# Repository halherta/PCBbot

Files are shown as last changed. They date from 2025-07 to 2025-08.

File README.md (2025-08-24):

# Introducing PCBbot!
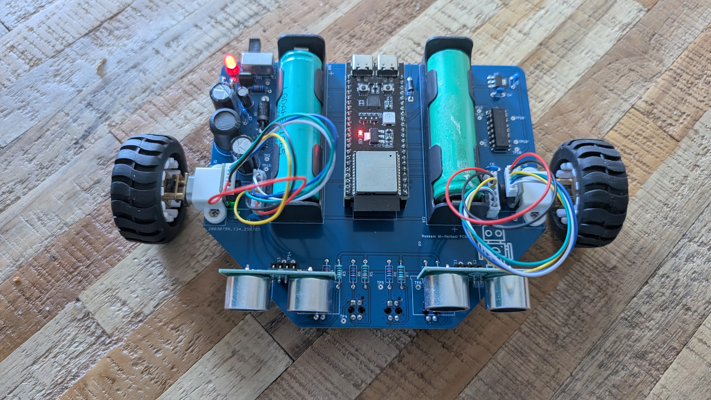
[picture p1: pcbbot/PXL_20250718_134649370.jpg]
pcbbot top view


The PCBBot leverages the PCB itself as the chassis. This reduces cost significantly. It also means that the two motors and the caster wheel would have to be mounted on the PCB itself, in addition to the batteries and all the other components...

For more info have a look at the write up on my [blog entry](https://hussamtalkstech.com/introducing-pcbbot/)

In this Github repo, you'll find my PCBBot KiCAD PCB design freely available (MIT License) along with a Digikey bill of materials (BOM) (caster wheel, motor brackets and motors not included) and MicroPython code. I’m also providing my [custom symbol and footprint libraries in this repo](https://github.com/halherta/mykicadlibrary). Feel free to make your own version of the PCBBot as is or modify it to suit your needs. Have fun!

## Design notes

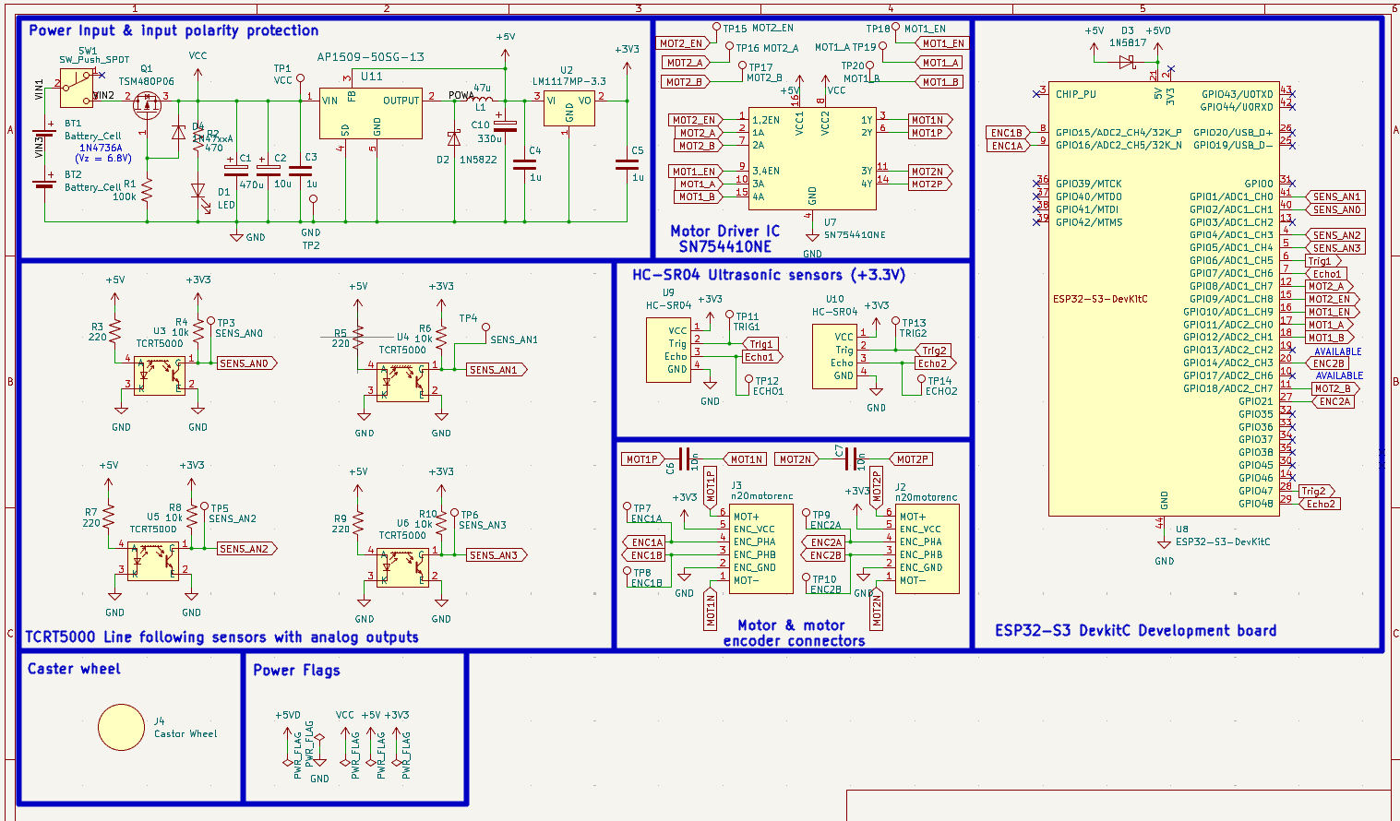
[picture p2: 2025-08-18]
pcbbot/pcbbot_schem.png

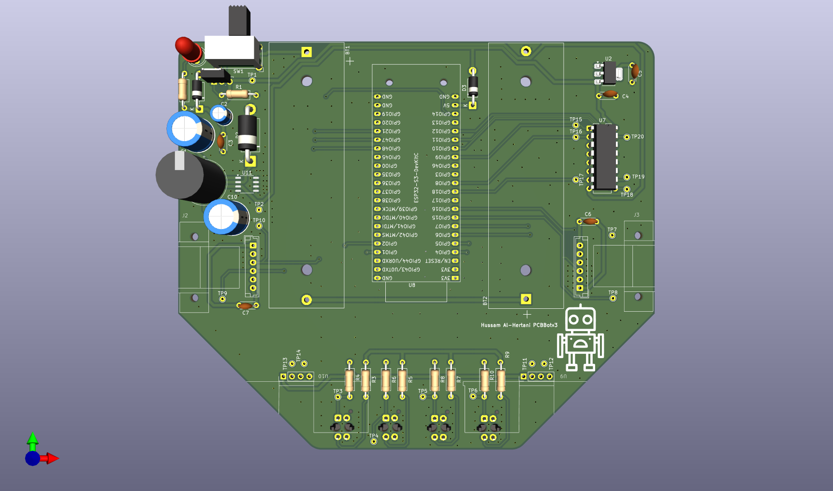
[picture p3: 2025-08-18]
pcbbot/PCBbot.png

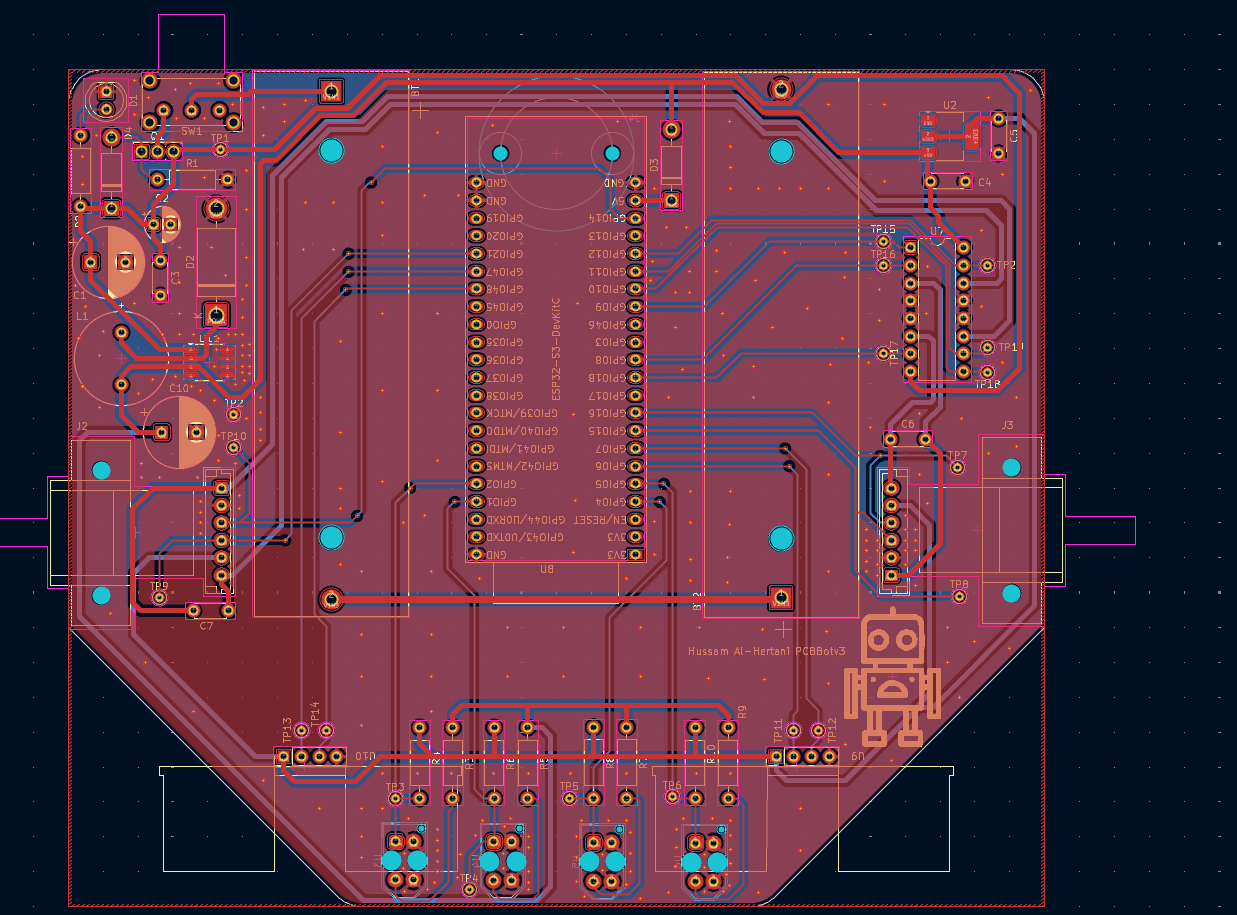
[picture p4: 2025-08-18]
pcbbot/pcbbotpcb.png

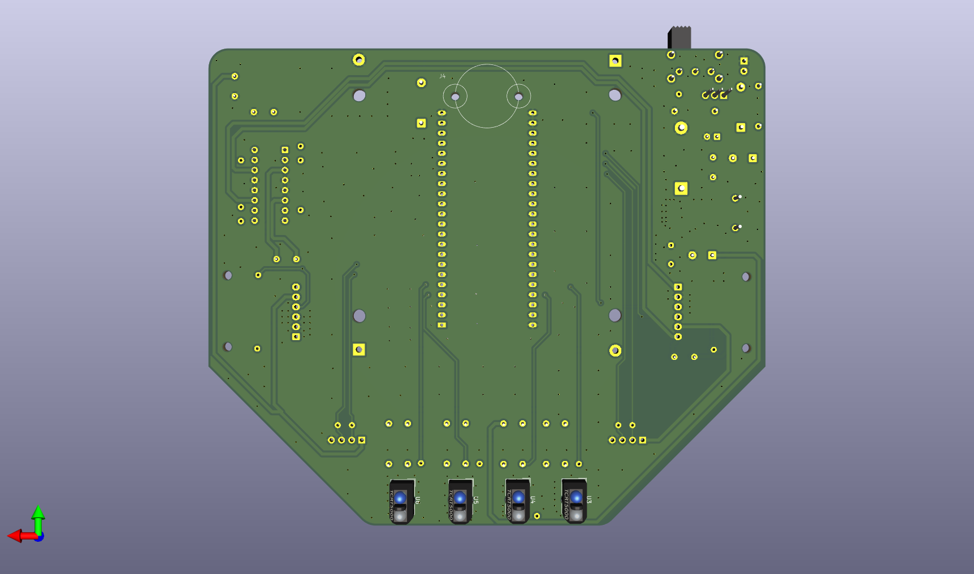
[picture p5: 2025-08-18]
pcbbot/PCBbot2.png

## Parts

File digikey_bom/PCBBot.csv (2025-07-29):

Index | Manufacturer Part Number | Manufacturer Name | Description | Availability | Stock Status | Attrition % | Requested Quantity 1 | Pack Quantity 1 | Pack Type 1 | Digi-Key Part Number 1 | Unit Price 1 | Extended Price 1 | Minimum Order Quantity 1 | Product Notes
1 | EHR-6 | JST Sales America Inc. | CONN RCPT HSG 6POS 2.50MM | 287,103 | In Stock
2 | B6B-EH-A | JST Sales America Inc. | CONN HEADER VERT 6POS 2.5MM | 10,232 | In Stock |  | 4 | 4 | Bulk | 455-1615-ND | 0.27000 | $1.08 | 1
3 | ESP32-S3-DEVKITC-1-N8R8 | Espressif Systems | ESP32-S3-WROOM-1-N8R8 DEV BRD | 0 | Normally Stocking
4 | SN754410NE | Texas Instruments | IC HALF-H DRIVER 36V 16-PDIP | 5,366 | In Stock |  | 1 | 1 | Tube | 296-9911-5-ND | 4.52000 | $4.52 | 1
5 | EG1224 | E-Switch | SWITCH SLIDE SPDT 500MA 15V | 5,229 | In Stock |  | 1 | 1 | Bulk | EG2585-ND | 1.48000 | $1.48 | 1
6 | PPPC221LFBN-RC | Sullins Connector Solutions | CONN HDR 22POS 0.1 GOLD PCB | 2,121 | In Stock |  | 2 | 2 | Tray | S7055-ND | 1.78000 | $3.56 | 1
7 | TCRT5000 | Vishay Semiconductor Opto Division | SENSOR OPTO TRANS 15MM REFL PCB | 2,885 | In Stock |  | 5 | 5 | Tube | 751-1033-5-ND | 1.60400 | $8.02 | 1
8 | TSM480P06CH X0G | Taiwan Semiconductor Corporation | MOSFET P-CHANNEL 60V 20A TO251 | 3,349 | In Stock |  | 1 | 1 | Tube | TSM480P06CHX0G-ND | 1.80000 | $1.80 | 1
9 | WP7113ID | Kingbright | LED RED DIFFUSED T-1 3/4 T/H | 96,702 | In Stock |  | 1 | 1 | Bulk | 754-1264-ND | 0.32000 | $0.32 | 1
10 | MFR-25FRF52-100K | YAGEO | RES 100K OHM 1% 1/4W AXIAL | 80,329 | In Stock |  | 1 | 1 | Cut Tape (CT) | 13-MFR-25FRF52-100KCT-ND | 0.14000 | $0.14 | 1
11 | MFR-25FTE52-470R | YAGEO | RES 470 OHM 1% 1/4W AXIAL | 0 | Normally Stocking |  | 1 | 1 | Cut Tape (CT) | 13-MFR-25FTE52-470RCT-ND | 0.14000 | $0.14 | 1
12 | 35ZLH470MEFC10X16 | Rubycon | CAP ALUM 470UF 20% 35V RADIAL TH | 191,971 | In Stock |  | 1 | 1 | Bulk | 1189-1890-ND | 1.02000 | $1.02 | 1
13 | FG24X7R1H105KRT06 | TDK Corporation | CAP CER 1UF 50V X7R RADIAL | 57,348 | In Stock |  | 3 | 3 | Cut Tape (CT) | 445-173374-1-ND | 0.70000 | $2.10 | 1
14 | 1N4734A | onsemi | DIODE ZENER 5.6V 1W DO41 | 8,168 | In Stock |  | 1 | 1 | Bulk | 1N4734AFS-ND | 0.32000 | $0.32 | 1
15 | BK-18650-PC2 | MPD (Memory Protection Devices) | BATTERY HOLDER 18650 PC PIN | 2,467 | In Stock |  | 2 | 2 | Tray | BK-18650-PC2-ND | 4.76000 | $9.52 | 1
16 | EEU-EB1H100SH | Panasonic Electronic Components | CAP ALUM 10UF 20% 50V RADIAL TH | 384 | In Stock |  | 1 | 1 | Cut Tape (CT) | P19607CT-ND | 0.42000 | $0.42 | 1
17 | LM1117MPX-3.3/NOPB | Texas Instruments | IC REG LIN 3.3V 800MA SOT-223-4 | 22,991 | In Stock |  | 1 | 1 | Cut Tape (CT) | LM1117MPX-3.3/NOPBCT-ND | 1.55000 | $1.55 | 1
18 | 1N5817-T | Diodes Incorporated | DIODE SCHOTTKY 20V 1A DO41 | 58,119 | In Stock |  | 1 | 1 | Cut Tape (CT) | 1N5817DICT-ND | 0.32000 | $0.32 | 1
19 | MFR-25FRF52-10K | YAGEO | RES 10K OHM 1% 1/4W AXIAL | 118,267 | In Stock |  | 10 | 10 | Cut Tape (CT) | 13-MFR-25FRF52-10KCT-ND | 0.05600 | $0.56 | 1
20 | FG18X7R1H103KNT06 | TDK Corporation | CAP CER 10000PF 50V X7R RADIAL | 11,857 | In Stock |  | 2 | 2 | Cut Tape (CT) | 445-173264-1-ND | 0.30000 | $0.60 | 1
21 | PPPC041LFBN-RC | Sullins Connector Solutions | CONN HDR 4POS 0.1 GOLD PCB | 19,116 | In Stock |  | 2 | 2 | Box | S7037-ND | 0.55000 | $1.10 | 1
22 | 4007 | Adafruit Industries LLC | ULT SEN TX/RX 3V/5.5V | 273 | In Stock
23 | SEH-001T-P0.6 | JST Sales America Inc. | CONN SOCKET 22-30AWG CRIMP TIN | 77,300 | In Stock - Value Added
24 | AIUR-06-470K | Abracon LLC | FIXED IND 47UH 3.2A 63 MOHM TH | 2,962 | In Stock |  | 1 | 1 | Bulk | 535-13031-ND | 1.33000 | $1.33 | 1
25 | AP1509-50SG-13 | Diodes Incorporated | IC REG BUCK 5V 2A 8SOP | 38,507 | In Stock |  | 1 | 1 | Cut Tape (CT) | AP1509-50SGDICT-ND | 1.86000 | $1.86 | 1
26 | 1N5822RL | STMicroelectronics | DIODE SCHOTTKY 40V 3A DO201AD | 19,311 | In Stock |  | 1 | 1 | Cut Tape (CT) | 497-14742-1-ND | 0.37000 | $0.37 | 1
27 | LR1F220R | TE Connectivity Passive Product | RES 220 OHM 1% 0.6W AXIAL | 13,524 | In Stock |  | 10 | 10 | Cut Tape (CT) | 1712-LR1F220RCT-ND | 0.04300 | $0.43 | 1
28 | 35ZLH330MEFC10X12.5 | Rubycon | CAP ALUM 330UF 20% 35V RADIAL TH | 18,236 | In Stock |  | 1 | 1 | Bulk | 1189-1891-ND | 0.89000 | $0.89 | 1

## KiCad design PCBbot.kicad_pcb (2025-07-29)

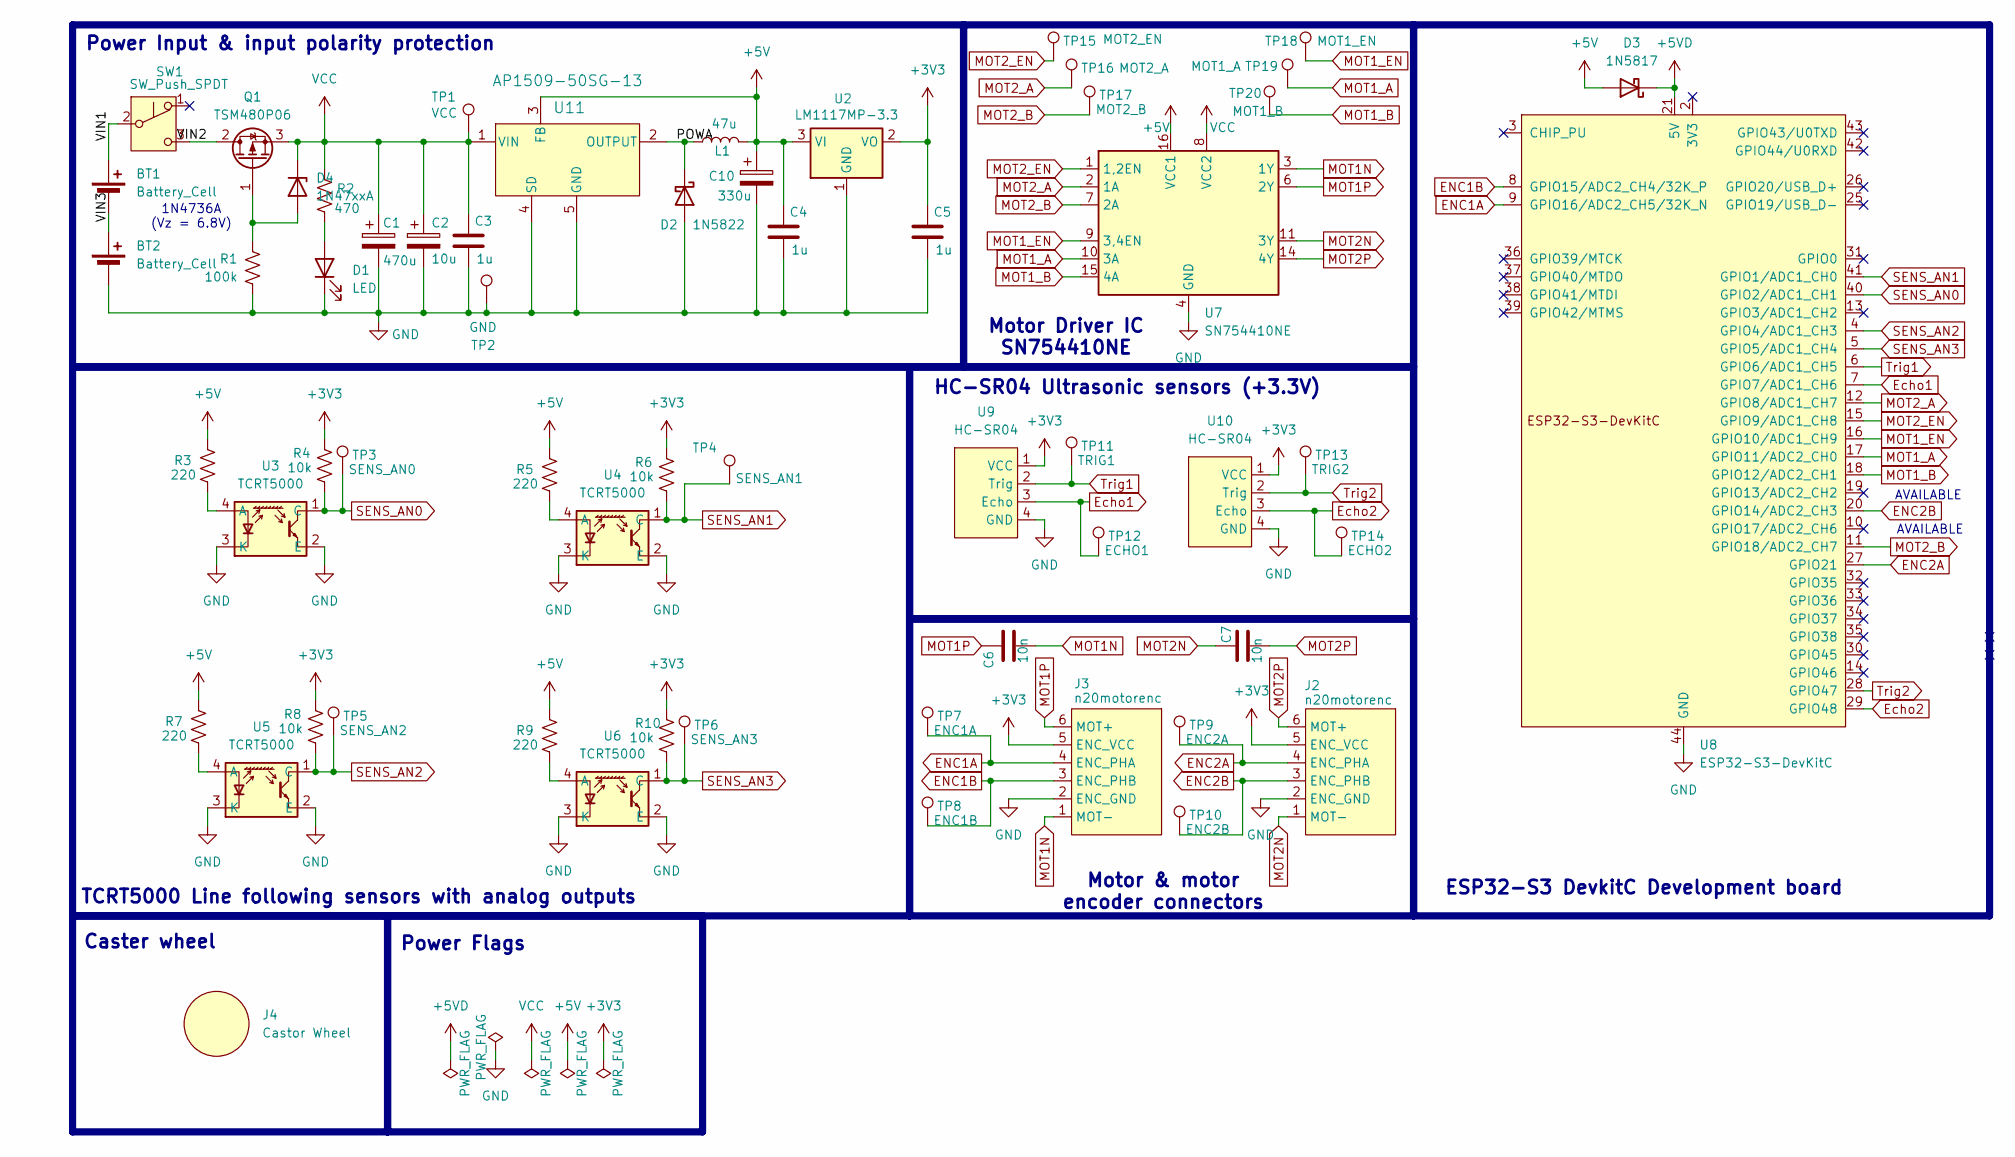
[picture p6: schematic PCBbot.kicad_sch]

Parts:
BT1, BT2: Battery_Cell; BatteryHolder_MPD_BK-18650-PC2
C1: 470u; CP_Radial_D10.0mm_P5.00mm
C2: 10u; CP_Radial_D5.0mm_P2.50mm
C3, C4, C5: 1u; C_Disc_D4.3mm_W1.9mm_P5.00mm
C6, C7: 10n; C_Disc_D4.3mm_W1.9mm_P5.00mm
C10: 330u; CP_Radial_D10.0mm_P5.00mm
D1: LED; LED_D5.0mm
D2: 1N5822; D_DO-201AD_P15.24mm_Horizontal
D3: 1N5817; D_DO-41_SOD81_P10.16mm_Horizontal
D4: 1N47xxA; D_DO-41_SOD81_P10.16mm_Horizontal
J2, J3: n20motorenc; n20motorencv2
J4: Castor Wheel; N20CasterSteelBall-Mini
L1: 47u; AIUR-06_ABRv2
Q1: TSM480P06; TO-251-3_Vertical
R1: 100k; R_Axial_DIN0207_L6.3mm_D2.5mm_P10.16mm_Horizontal
R2: 470; R_Axial_DIN0207_L6.3mm_D2.5mm_P10.16mm_Horizontal
R3, R5, R7, R9: 220; R_Axial_DIN0207_L6.3mm_D2.5mm_P10.16mm_Horizontal
R4, R6, R8, R10: 10k; R_Axial_DIN0207_L6.3mm_D2.5mm_P10.16mm_Horizontal
SW1: SW_Push_SPDT; SW_E-Switch_EG1224_SPDT_Angled
TP1: VCC; TestPoint_THTPad_D1.5mm_Drill0.7mm
TP2: GND; TestPoint_THTPad_D1.5mm_Drill0.7mm
TP3: SENS_AN0; TestPoint_THTPad_D1.5mm_Drill0.7mm
TP4: SENS_AN1; TestPoint_THTPad_D1.5mm_Drill0.7mm
TP5: SENS_AN2; TestPoint_THTPad_D1.5mm_Drill0.7mm
TP6: SENS_AN3; TestPoint_THTPad_D1.5mm_Drill0.7mm
TP7: ENC1A; TestPoint_THTPad_D1.5mm_Drill0.7mm
TP8: ENC1B; TestPoint_THTPad_D1.5mm_Drill0.7mm
TP9: ENC2A; TestPoint_THTPad_D1.5mm_Drill0.7mm
TP10: ENC2B; TestPoint_THTPad_D1.5mm_Drill0.7mm
TP11: TRIG1; TestPoint_THTPad_D1.5mm_Drill0.7mm
TP12: ECHO1; TestPoint_THTPad_D1.5mm_Drill0.7mm
TP13: TRIG2; TestPoint_THTPad_D1.5mm_Drill0.7mm
TP14: ECHO2; TestPoint_THTPad_D1.5mm_Drill0.7mm
TP15: MOT2_EN; TestPoint_THTPad_D1.5mm_Drill0.7mm
TP16: MOT2_A; TestPoint_THTPad_D1.5mm_Drill0.7mm
TP17: MOT2_B; TestPoint_THTPad_D1.5mm_Drill0.7mm
TP18: MOT1_EN; TestPoint_THTPad_D1.5mm_Drill0.7mm
TP19: MOT1_A; TestPoint_THTPad_D1.5mm_Drill0.7mm
TP20: MOT1_B; TestPoint_THTPad_D1.5mm_Drill0.7mm
U2: LM1117MP-3.3; SOT-223-3_TabPin2
U3, U4, U5, U6: TCRT5000; Vishay_TCRT5000
U7: SN754410NE; DIP-16_W7.62mm
U8: ESP32-S3-DevKitC
U9, U10: HC-SR04
U11: AP1509-50SG-13; SOP-8_3.9x4.9mm_P1.27mm

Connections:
+3V3: C5.1, J2.5 (ENC_VCC), J3.5 (ENC_VCC), R4.1, R6.1, R8.1, R10.1, U2.2 (VO), U9.1 (VCC), U10.1 (VCC)
+5V: C4.1, C10.1, D3.2 (A), L1.2, R3.1, R5.1, R7.1, R9.1, U2.3 (VI), U7.16 (VCC1), U11.3 (FB)
+5VD: D3.1 (K), U8.21 (5V)
/POWA: D2.1 (K), L1.1, U11.2 (OUTPUT)
/VIN1: BT1.1 (+), SW1.2 (B)
/VIN2: Q1.2 (D), SW1.3 (C)
/VIN3: BT1.2 (-), BT2.1 (+)
ENC1A: J3.4 (ENC_PHA), TP7.1, U8.9 (GPIO16/ADC2_CH5/32K_N)
ENC1B: J3.3 (ENC_PHB), TP8.1, U8.8 (GPIO15/ADC2_CH4/32K_P)
ENC2A: J2.4 (ENC_PHA), TP9.1, U8.27 (GPIO21)
ENC2B: J2.3 (ENC_PHB), TP10.1, U8.20 (GPIO14/ADC2_CH3)
Echo1: TP12.1, U8.7 (GPIO7/ADC1_CH6), U9.3 (Echo)
Echo2: TP14.1, U8.29 (GPIO48), U10.3 (Echo)
GND: BT2.2 (-), C1.2, C2.2, C3.2, C4.2, C5.2, C10.2, D1.1 (K), D2.2 (A), J2.2 (ENC_GND), J3.2 (ENC_GND), R1.2, TP2.1, U2.1 (GND), U3.2 (E), U3.3 (K), U4.2 (E), U4.3 (K), U5.2 (E), U5.3 (K), U6.2 (E), U6.3 (K), U7.4 (GND), U7.5 (GND), U7.12 (GND), U7.13 (GND), U8.22 (GND), U8.23 (GND), U8.24 (GND), U8.44 (GND), U9.4 (GND), U10.4 (GND), U11.4 (SD), U11.5 (GND), U11.6 (GND), U11.7 (GND), U11.8 (GND)
MOT1N: C6.2, J3.1 (MOT-), U7.3 (1Y)
MOT1P: C6.1, J3.6 (MOT+), U7.6 (2Y)
MOT1_A: TP19.1, U7.10 (3A), U8.17 (GPIO11/ADC2_CH0)
MOT1_B: TP20.1, U7.15 (4A), U8.18 (GPIO12/ADC2_CH1)
MOT1_EN: TP18.1, U7.9 (3,4EN), U8.16 (GPIO10/ADC1_CH9)
MOT2N: C7.1, J2.1 (MOT-), U7.11 (3Y)
MOT2P: C7.2, J2.6 (MOT+), U7.14 (4Y)
MOT2_A: TP16.1, U7.2 (1A), U8.12 (GPIO8/ADC1_CH7)
MOT2_B: TP17.1, U7.7 (2A), U8.11 (GPIO18/ADC2_CH7)
MOT2_EN: TP15.1, U7.1 (1,2EN), U8.15 (GPIO9/ADC1_CH8)
unnamed: D1.2 (A), R2.2
unnamed: D4.2 (A), Q1.1 (G), R1.1
unnamed: R3.2, U3.4 (A)
unnamed: R5.2, U4.4 (A)
unnamed: R7.2, U5.4 (A)
unnamed: R9.2, U6.4 (A)
SENS_AN0: R4.2, TP3.1, U3.1 (C), U8.40 (GPIO2/ADC1_CH1)
SENS_AN1: R6.2, TP4.1, U4.1 (C), U8.41 (GPIO1/ADC1_CH0)
SENS_AN2: R8.2, TP5.1, U5.1 (C), U8.4 (GPIO4/ADC1_CH3)
SENS_AN3: R10.2, TP6.1, U6.1 (C), U8.5 (GPIO5/ADC1_CH4)
Trig1: TP11.1, U8.6 (GPIO6/ADC1_CH5), U9.2 (Trig)
Trig2: TP13.1, U8.28 (GPIO47), U10.2 (Trig)
VCC: C1.1, C2.1, C3.1, D4.1 (K), Q1.3 (S), R2.1, TP1.1, U7.8 (VCC2), U11.1 (VIN)

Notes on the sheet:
HC-SR04 Ultrasonic sensors (+3.3V)
Power Input & input polarity protection
Motor Driver IC SN754410NE
Motor & motor encoder connectors
AVAILABLE
Caster wheel
1N4736A (Vz = 6.8V)
ESP32-S3 DevkitC Development board
TCRT5000 Line following sensors with analog outputs
Power Flags

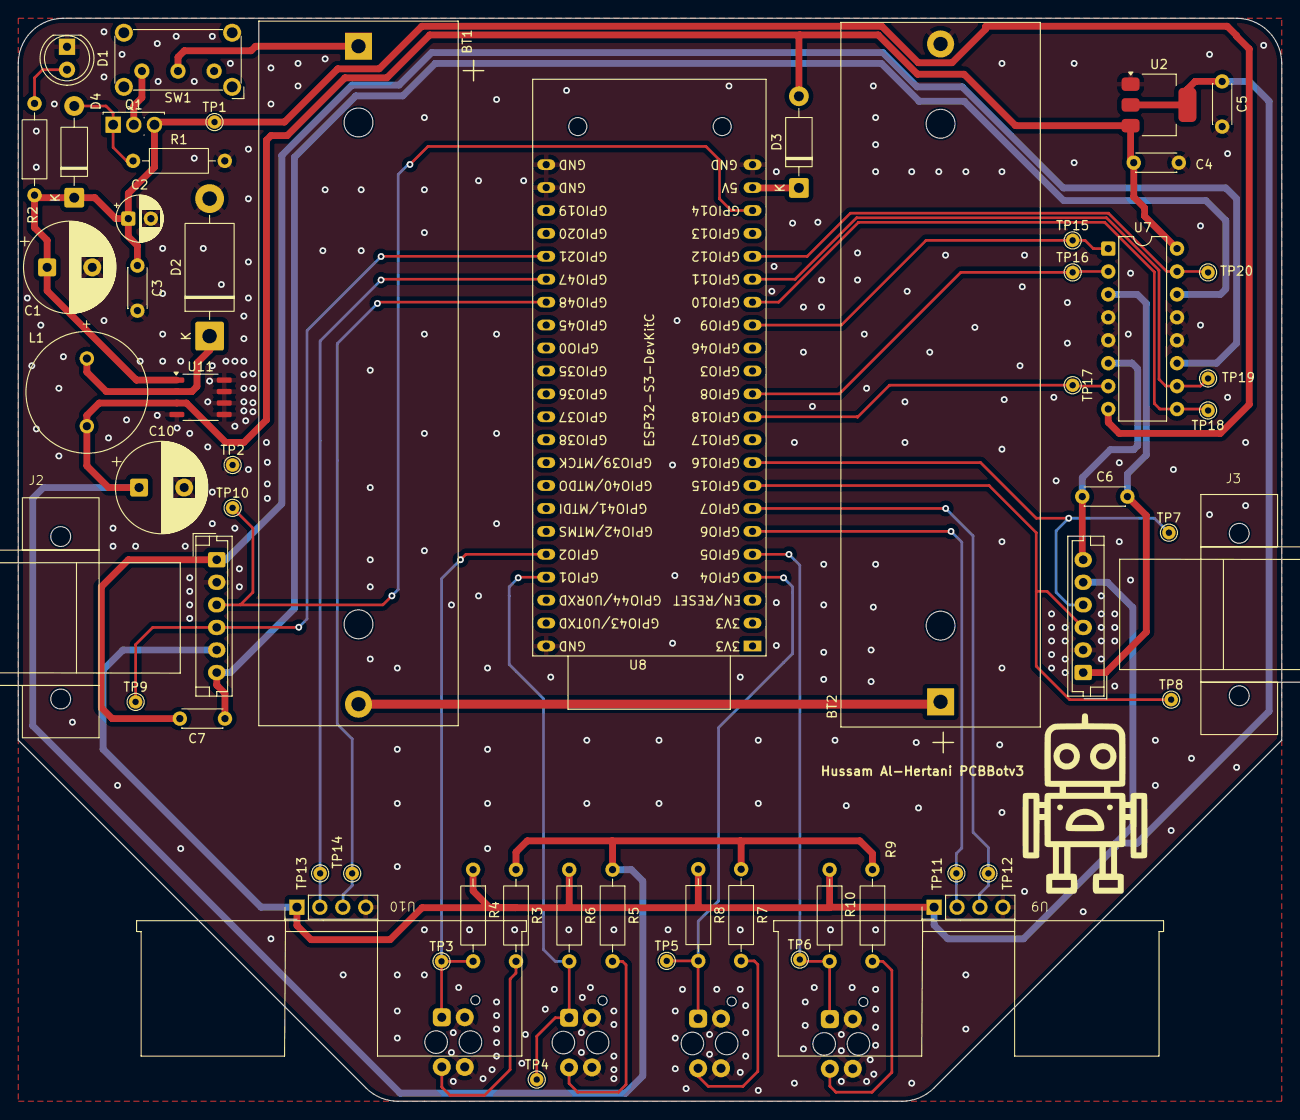
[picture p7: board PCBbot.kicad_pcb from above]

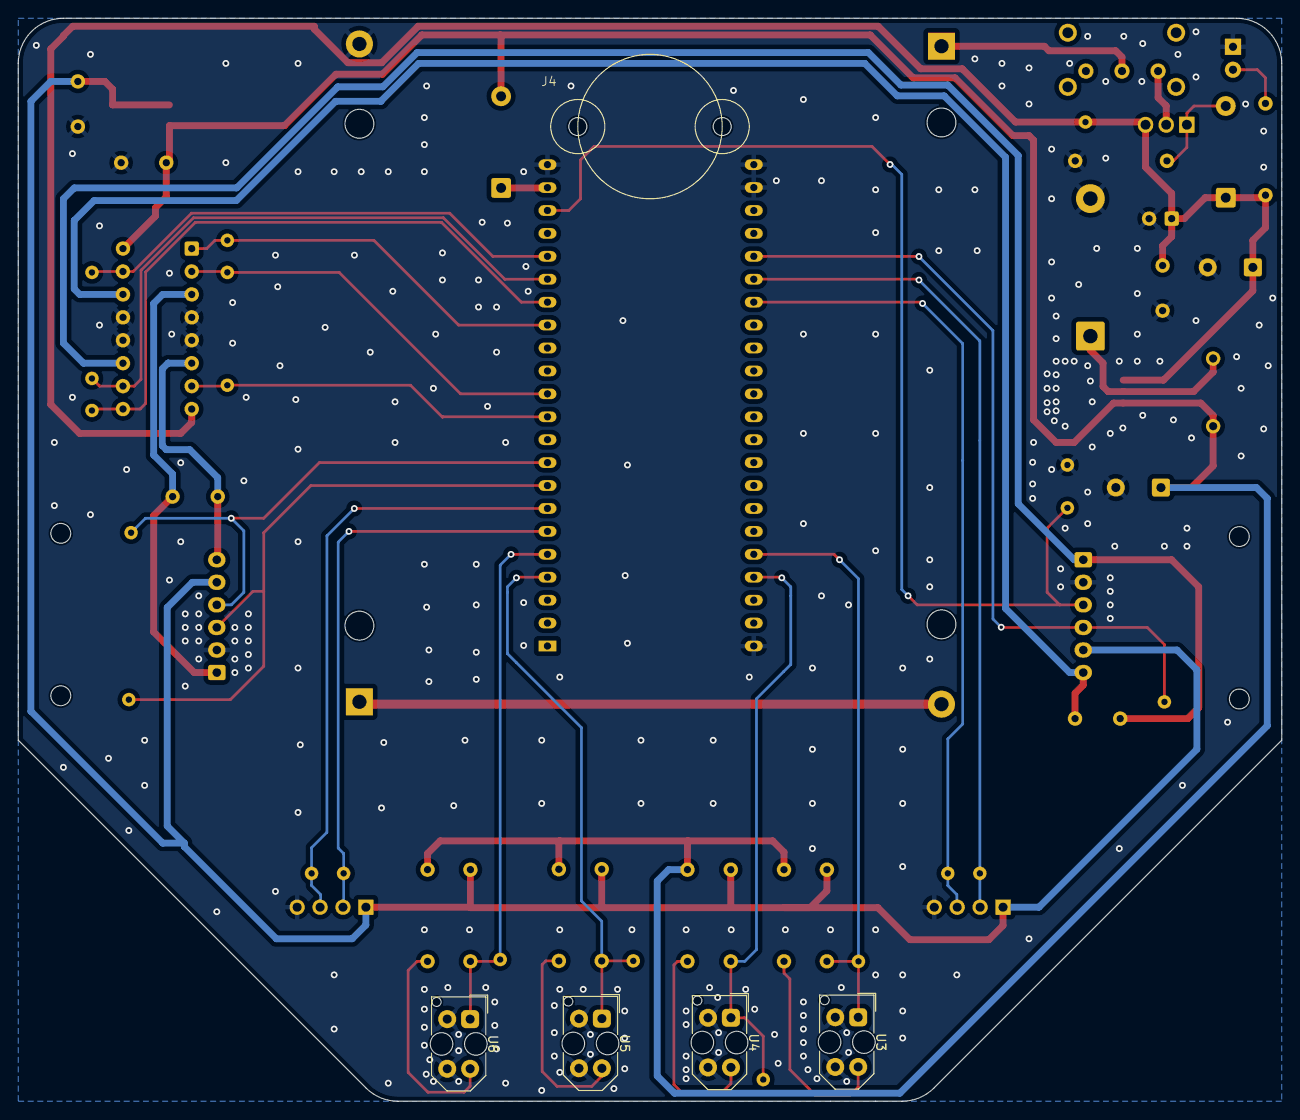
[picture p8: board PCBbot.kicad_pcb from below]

Board: 2 copper layers, 140.0 x 120.0 mm, 60 parts (5 on the bottom side), 37 nets.

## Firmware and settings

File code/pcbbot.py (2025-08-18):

import time
from machine import Pin, PWM, ADC, time_pulse_us

class RobotDirection:
    STP = 0
    FWD = 1
    REV = 2
    BRK = 3
    LEFT = 4
    CKW = 4
    RIGHT = 5
    CCKW = 5
    
class MotorDirection:
    STP = 0
    FWD = 1
    REV = 2
    BRK = 3
        
class PCBBotPins:
    AN0 = 2
    AN1 = 1
    AN2 = 4
    AN3 = 5
    TRG1 = 6
    ECH1 = 7
    TRG2 = 47
    ECH2 = 48
    MOT1A = 11
    MOT1B = 12
    MOT1EN = 10
    MOT1ENCA = 16
    MOT1ENCB = 15
    MOT2A = 8
    MOT2B = 18
    MOT2EN = 9
    MOT2ENCA = 21
    MOT2ENCB = 14
    
class PCBBot:
    def __init__(self):
        self.mot1a = Pin(PCBBotPins.MOT1A, Pin.OUT)
        self.mot1b = Pin(PCBBotPins.MOT1B, Pin.OUT)
        self.mot2a = Pin(PCBBotPins.MOT2A, Pin.OUT)
        self.mot2b = Pin(PCBBotPins.MOT2B, Pin.OUT)
        self.mot1en = PWM(Pin(PCBBotPins.MOT1EN), freq=500, duty_u16=65535)
        self.mot2en = PWM(Pin(PCBBotPins.MOT2EN), freq=500, duty_u16=65535)
        
        self.ech1 = Pin(PCBBotPins.ECH1,mode=Pin.IN, pull=None)
        self.trg1 = Pin(PCBBotPins.TRG1, mode=Pin.OUT, pull=None)
        
        self.ech2 = Pin(PCBBotPins.ECH2,mode=Pin.IN, pull=None)
        self.trg2 = Pin(PCBBotPins.TRG2, mode=Pin.OUT, pull=None)
        
        self.an0 = ADC(PCBBotPins.AN0)
        self.an1 = ADC(PCBBotPins.AN1)
        self.an2 = ADC(PCBBotPins.AN2)
        self.an3 = ADC(PCBBotPins.AN3)
        
        self.obstacle_avoidance_mode=False
        self.line_following_mode=False
        
    def mot1_move(self,direction=MotorDirection.STP, speed=0.5):
        if direction == MotorDirection.BRK :
            self.mot1a.value(1)
            self.mot1b.value(1)
        elif direction == MotorDirection.FWD :
            self.mot1a.value(0)
            self.mot1b.value(1)
        elif direction == MotorDirection.REV :
            self.mot1a.value(1)
            self.mot1b.value(0)
        else:
            self.mot1a.value(0)
            self.mot1b.value(0)
    
        self.mot1en.duty_u16(int(speed*65535))
        
    def mot2_move(self,direction=MotorDirection.STP, speed=0.5):
        if direction == MotorDirection.BRK :
            self.mot2a.value(1)
            self.mot2b.value(1)
        elif direction == MotorDirection.FWD :
            self.mot2a.value(1)
            self.mot2b.value(0)
        elif direction == MotorDirection.REV :
            self.mot2a.value(0)
            self.mot2b.value(1)
        else:
            self.mot2a.value(0)
            self.mot2b.value(0)
        
        self.mot2en.duty_u16(int(speed*65535))   
    
    def robot_move(self, direction=RobotDirection.STP,speedmot1=0.5, speedmot2=0.5):
        if direction == RobotDirection.BRK :
            self.mot1_move(MotorDirection.BRK, 1.0)
            self.mot2_move(MotorDirection.BRK, 1.0)
        elif direction == RobotDirection.FWD :
            self.mot1_move(MotorDirection.FWD, speedmot1)
            self.mot2_move(MotorDirection.FWD, speedmot2)
        elif direction == RobotDirection.REV :
            self.mot1_move(MotorDirection.REV, speedmot1)
            self.mot2_move(MotorDirection.REV, speedmot2)
        elif direction == RobotDirection.RIGHT :
            self.mot1_move(MotorDirection.FWD, speedmot1)
            self.mot2_move(MotorDirection.REV, speedmot2)
        elif direction == RobotDirection.LEFT :
            self.mot1_move(MotorDirection.REV, speedmot1)
            self.mot2_move(MotorDirection.FWD, speedmot2)
        else:
            self.mot1_move(MotorDirection.STP, 1.0)
            self.mot2_move(MotorDirection.STP, 1.0)
    
    def robot_move_with_delay(self, direction=RobotDirection.STP, delay_ms=100, speedmot1=0.5, speedmot2=0.5):
        self.robot_move(direction,speedmot1, speedmot2)
        time.sleep_ms(delay_ms)
        self.robot_move(RobotDirection.BRK,1.0, 1.0)
        time.sleep_ms(100)
        
        
    def read_line_sensors(self):
        return self.an0.read_uv()/1.0e6, self.an1.read_uv()/1.0e6, self.an2.read_uv()/1.0e6, self.an3.read_uv()/1.0e6

    def ultrasonic_left(self,timeout_us=30000):
        self.trg1.value(0) # Stabilize the sensor
        time.sleep_ms(1)
        # Send a 10us pulse.
        self.trg1.value(1)
        time.sleep_us(10)
        self.trg1.value(0)
        
        pulse_time = time_pulse_us(self.ech1, 1,timeout_us)
        if pulse_time == -2 or pulse_time == -1 :
            print("timeout")
            return pulse_time
        else:
            mm = pulse_time * 100 // 582
            return mm
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

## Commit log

2025-07-29 added digikey bom
    [PCBBot.csv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]
2025-08-18 added sample micropython code
